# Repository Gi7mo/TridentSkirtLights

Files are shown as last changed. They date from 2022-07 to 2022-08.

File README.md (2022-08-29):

# Voron Trident Skirt Lights #

**BOM**
|Part NO.  |Qty  |LCSC  |
|--|--|--|
| Conn_01x03 | 2 | C131339 |
| WS2812-2020 | 12 | C965555 |

**Assembly**
- Order the pcb at e.g. [pcbway](https://www.pcbway.com/project/shareproject/Trident_Skirt_Lights_6d030a0b.html) or [jlcpcb](https://jlcpcb.com/) (you need two for one printer)
    - Or just contact me via Discord "Gi7mo!#4618" i stil have some assembled boards left from my prototyping
- Order the parts at e.g. [lcsc](https://www.lcsc.com/)
- Print the new skirts (You WILL need supports)
- Print the new logo inserts (You WILL need supports)
- in the meantime, assemble the pcb
- Push in the new logo inserts in your skirts
- Push the pcb into the logo insert, no additional fasteing required
- Wire up the pcbs to your controller
- Add them as normal neopixels to your config
```
[neopixel my_skirts]
pin: YOUR_NEOPIXEL_PIN
chain_count: 24
initial_RED: 1.0
```

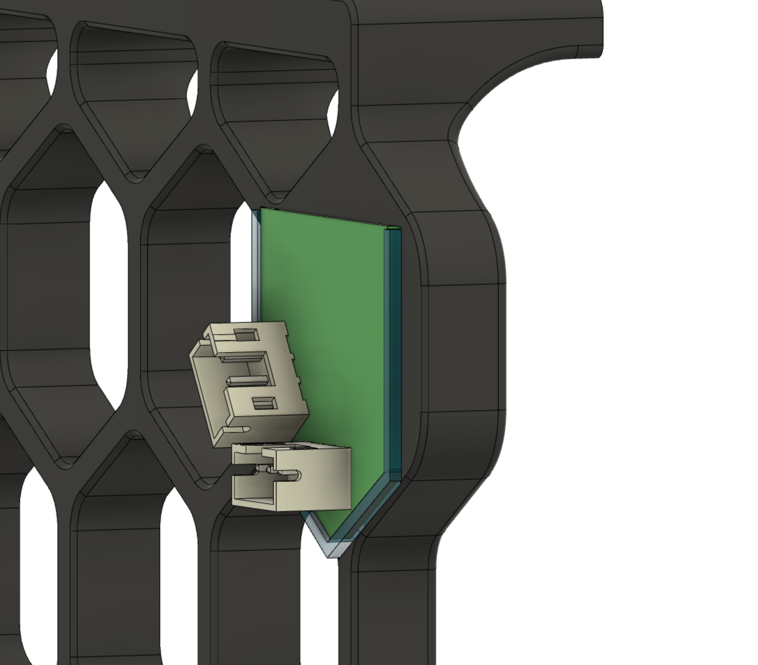
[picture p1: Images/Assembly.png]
Assembly
- 
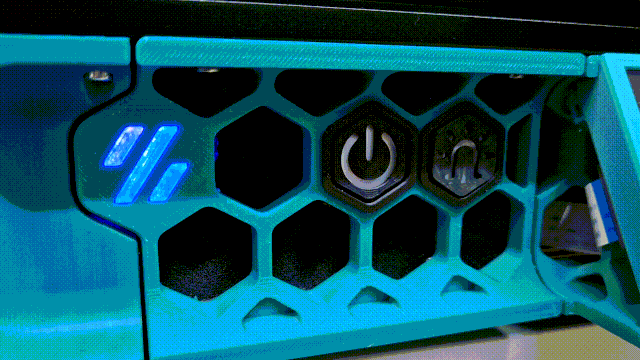
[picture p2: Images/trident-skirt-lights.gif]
Animated
- 

## Troubleshooting
- Problem: My Leds showing Random colors
    - Solution: Add a ~400Ω Resistor on the data line

## Notes
- You can contact me via Discord "Gi7mo!#4618"
- This readme file contains Amazon Associate, Aliexpress affiliate, PCBWay affiliate links. I make a comission on qualifying purchases.
- This project does not come with any warranty, if you choose to build/use one, you are doing this at your own risk!

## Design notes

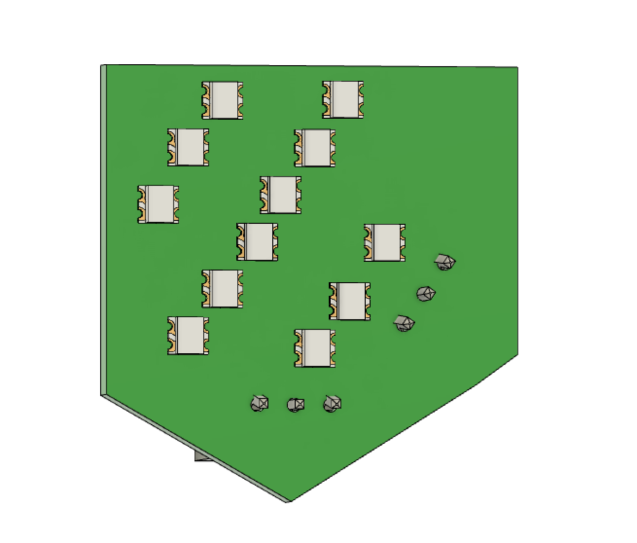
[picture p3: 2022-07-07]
Images/pcb.png

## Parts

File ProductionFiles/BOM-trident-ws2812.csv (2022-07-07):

Comment | Designator | Footprint | LCSC
Conn_01x03 | IN1,OUT1 | JST_PH_B3B-PH-K_1x03_P2.00mm_Vertical | C131339
WS2812-2020 | U1,U10,U11,U12,U2,U3,U4,U5,U6,U7,U8,U9 | LED_WS2812-2020 | C965555

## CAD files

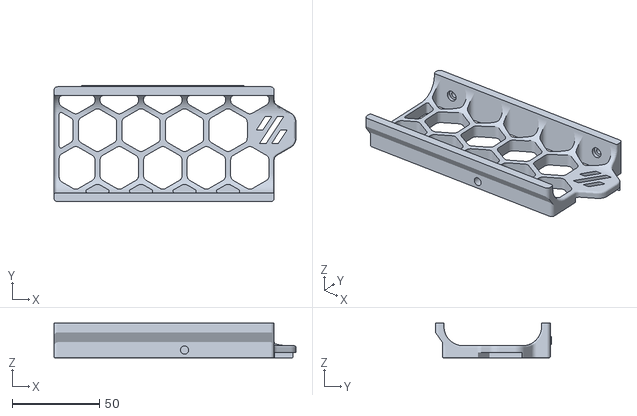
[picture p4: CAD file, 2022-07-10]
STL/front_skirt_a_300.stl
139.0 x 66.8 x 20.0

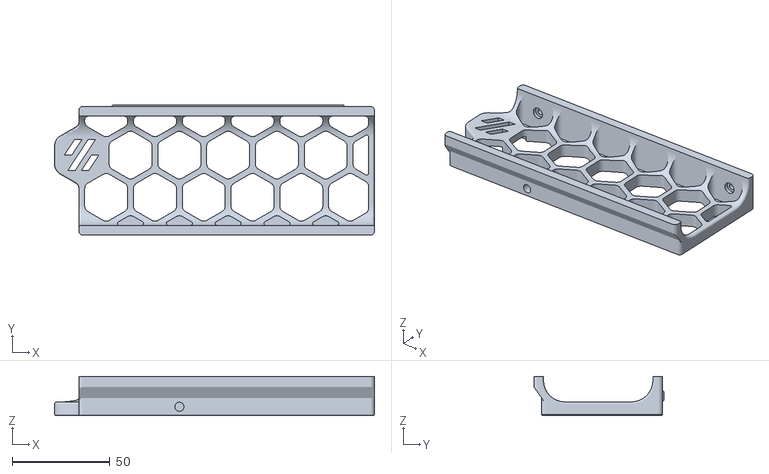
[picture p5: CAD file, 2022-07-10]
STL/front_skirt_b_350.stl
164.0 x 66.8 x 20.0

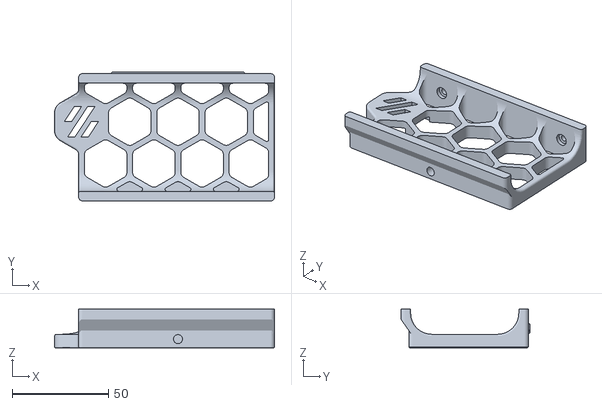
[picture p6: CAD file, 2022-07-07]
STL/front_skirt_b_250.stl
114.0 x 66.8 x 20.0

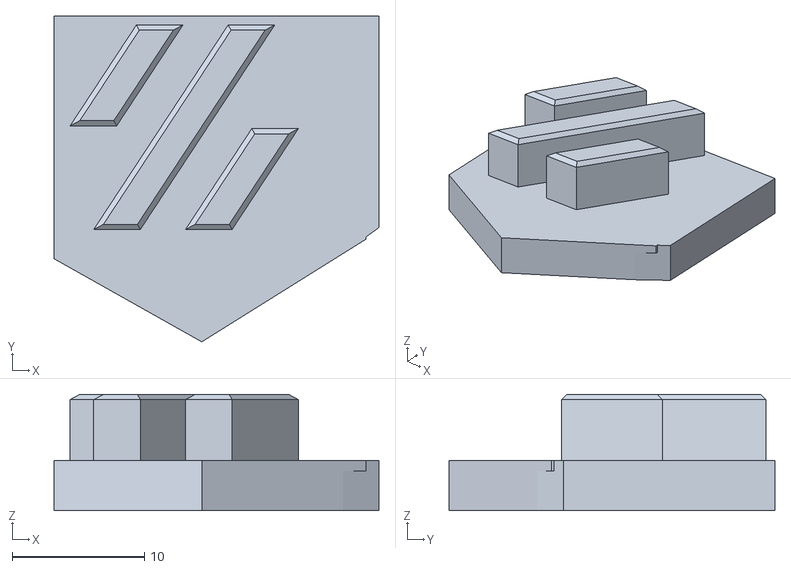
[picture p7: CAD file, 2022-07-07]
STL/[c]_skirt_logo_x2.stl
24.6 x 24.7 x 8.80

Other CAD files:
STL/front_skirt_b_300.stl
STL/front_skirt_a_350.stl
STL/front_skirt_a_250.stl
CAD/left.f3d
CAD/right.f3d

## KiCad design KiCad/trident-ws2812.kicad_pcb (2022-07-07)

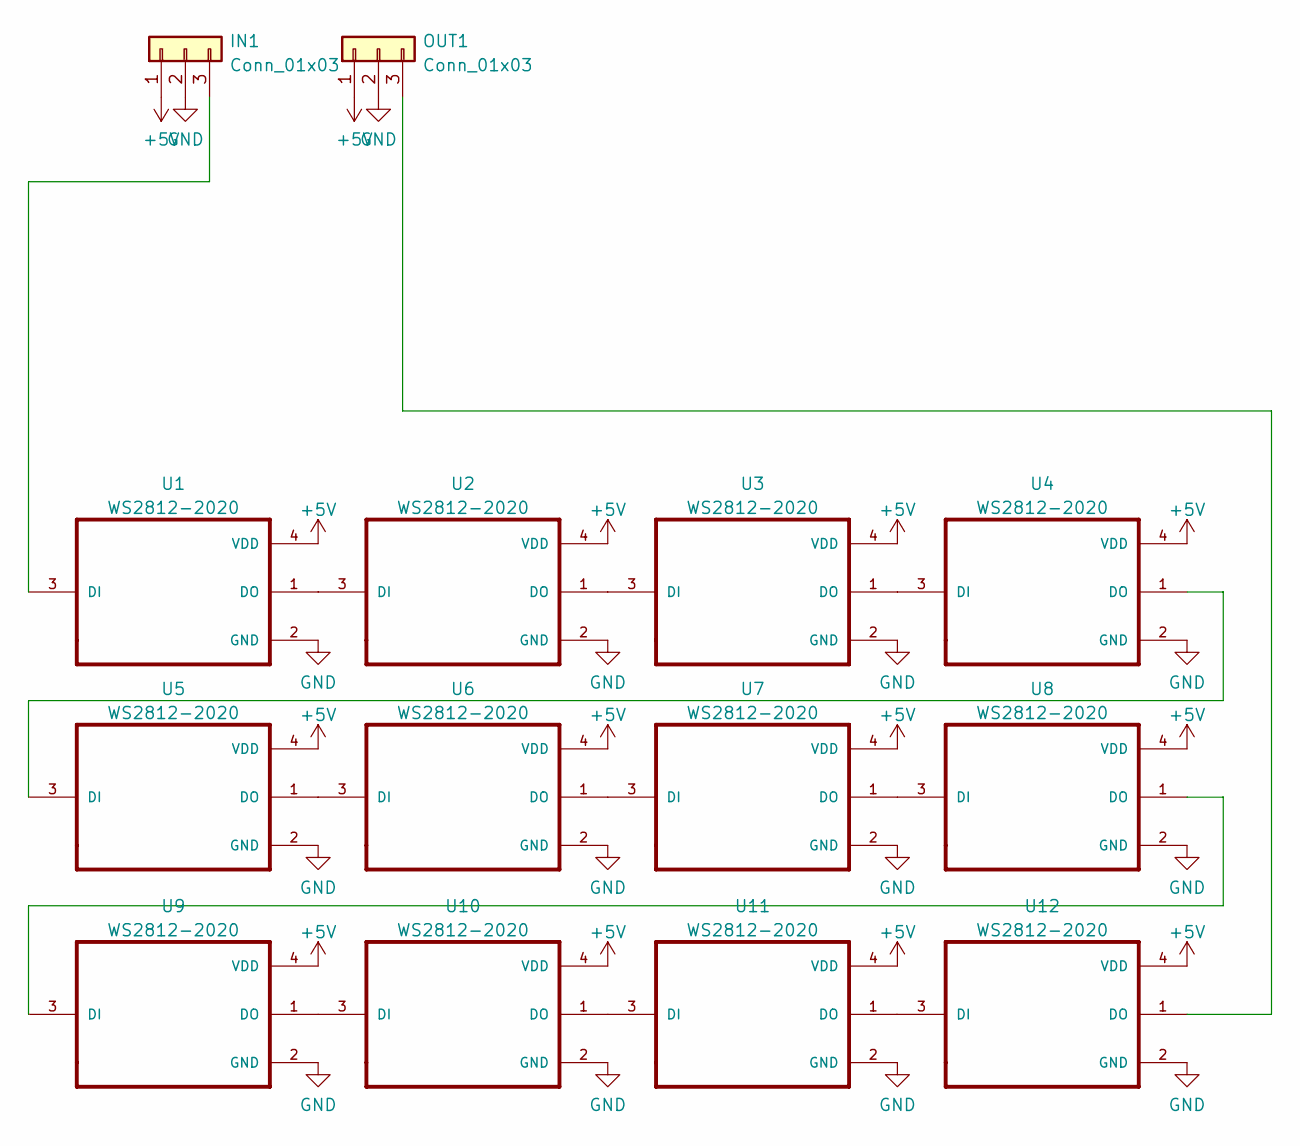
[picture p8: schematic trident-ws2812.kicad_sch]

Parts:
IN1: Conn_01x03; JST_PH_B3B-PH-K_1x03_P2.00mm_Vertical; LCSC C131339
OUT1: Conn_01x03; JST_PH_B3B-PH-K_1x03_P2.00mm_Vertical; LCSC C131339
U1, U2, U4, U5, U6, U7, U8, U9, U10, U11, U12: WS2812-2020; LED_WS2812-2020; LCSC C965555
U3: WS2812-2020; LED_WS2812-2020; LCSCL C965555

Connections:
+5V: IN1.1, OUT1.1, U1.4 (VDD), U2.4 (VDD), U3.4 (VDD), U4.4 (VDD), U5.4 (VDD), U6.4 (VDD), U7.4 (VDD), U8.4 (VDD), U9.4 (VDD), U10.4 (VDD), U11.4 (VDD), U12.4 (VDD)
GND: IN1.2, OUT1.2, U1.2 (GND), U2.2 (GND), U3.2 (GND), U4.2 (GND), U5.2 (GND), U6.2 (GND), U7.2 (GND), U8.2 (GND), U9.2 (GND), U10.2 (GND), U11.2 (GND), U12.2 (GND)
unnamed: IN1.3, U1.3 (DI)
unnamed: OUT1.3, U12.1 (DO)
unnamed: U1.1 (DO), U2.3 (DI)
unnamed: U2.1 (DO), U3.3 (DI)
unnamed: U3.1 (DO), U4.3 (DI)
unnamed: U4.1 (DO), U5.3 (DI)
unnamed: U5.1 (DO), U6.3 (DI)
unnamed: U6.1 (DO), U7.3 (DI)
unnamed: U7.1 (DO), U8.3 (DI)
unnamed: U8.1 (DO), U9.3 (DI)
unnamed: U10.1 (DO), U11.3 (DI)
unnamed: U9.1 (DO), U10.3 (DI)
unnamed: U11.1 (DO), U12.3 (DI)

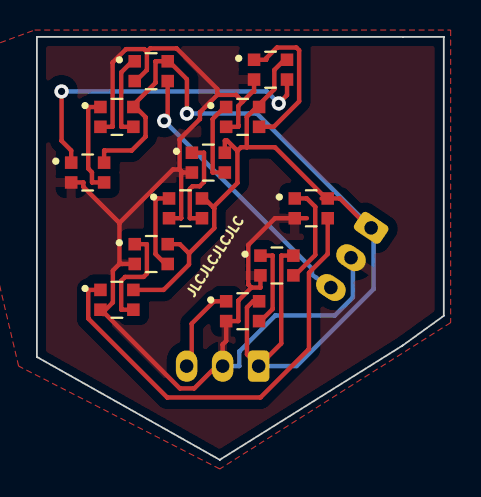
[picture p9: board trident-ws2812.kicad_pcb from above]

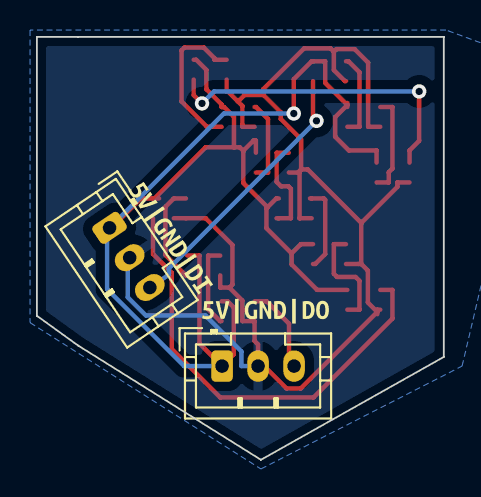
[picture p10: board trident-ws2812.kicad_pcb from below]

Board: 2 copper layers, 22.6 x 23.5 mm, 16 parts (4 on the bottom side), 15 nets.

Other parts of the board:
kibuzzard-62A46B00: G***; kibuzzard-62A46B00
kibuzzard-62A46BC2: G***; kibuzzard-62A46BC2

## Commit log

2022-07-10 add 300 and 350 skirts
    [front_skirt_a_300.stl, front_skirt_a_350.stl, front_skirt_b_300.stl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]
2024-08-25 add skirt cad
    [left.f3d, right.f3d]
